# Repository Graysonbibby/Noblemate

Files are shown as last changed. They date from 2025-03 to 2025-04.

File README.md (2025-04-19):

# NobleMate (Automated Voice Controlled Chess Game)
- ### Project Contributors Include: Saud Amjad, Grayson Bibby, Hamzah Nadeem, Kunj Patel, Megh Patel, Nihar Trivedi

**Project Description:** Over the past semester, our team, NobleMate, had designed a voice-controlled, completely automated chess game system against Stockfish.  Our focus being hands-free control with minimal intervention from the user, utilizing an X-Y Coordinate Mechanical Gantry system with an electromagnet for autonomous movement. Each chess piece was 3D printed with slots for magnets at the base. You say your moves by speaking into the microphone when prompted, saying "Pawn from C2 to C3" and this data is serially communicated to the gantry system. You can select your colour (White/Black) and can choose a difficulty (Easy, Medium, Difficult, Insane)
# --------------------------------------------------
- Note: main.cpp and Makefile are given as well
### Documentation + Comprehensive BOM

- Final Design Specification Report Outlines full design implementation + design considerations 
- Page 60 outlines the full BOM of the project

### PCB (Altium Designer files)
- PCB design for a 12V/5V DC-DC buck converter in the shape of a chess piece. You are going from the 12V wall supply and powering the Arduino Uno, Raspberry Pi, and Electromagnet all from this PCB

### Voice Recognition (Python - Requires SpeechRecognition, google-cloud-speech, difflib)

- For the recognizer: Google Cloud Speech-To-Text v1 REST API or Google Web Speech API is sufficient for this project. Google Cloud will require Application Default Credentials to be defined on your system. This is easily doable with a Google Account and downloading Google SDK. 
- All of the voice recognition code is under "chess_voice.py" in the Final Code Folder and the function is then called in a C++ environment using "voiceCommand.cpp" (Requires "voiceCommand.hpp")
- This will require WiFi and the code will be on the Raspberry Pi

### Gantry Movement (Embedded C++ - Code for Arduino Uno)

- This code is developed for the required stepper motor control for the Gantry System. The code was developed using the Arduino Uno IDE

### Chess Game Logic and Functionality (C++)

- Largely developed this ourself and the required code is in the Final Code folder. 
- REST API for Stockfish was used 
- We used https://github.com/awsomeCStutorials/chess-game/blob/master/README.md as a reference for a starting point, but wrote all the C++ code ourselves
- Files include (chess_board, stockfish_service, FENConverter, main, pieces)
- Stockfish is running locally on the Raspberry Pi

### Serial Communication 

- This project utilized a Raspberry Pi 3 Model B for the Chess Logic/Game functionality and an Arduino Uno for the Gantry System Control
- Sends a 7 digit number to the Arduino -> First four digits are the initial and end coordinates of the piece of interest, Final three digits are corresponding flags for special moves, etc.

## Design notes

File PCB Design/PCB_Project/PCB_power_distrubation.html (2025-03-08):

Altium customize

# Board Information Report

Date: | | 2025-03-07
Time: | | 11:34:49 PM
Elapsed Time: | | 00:00:00
Filename: | | C:\Users\Kunj_\OneDrive\Documents\GitHub\Noblemate\PCB Design\PCB_Project\PCB_power_distrubation.PcbDoc
Units: | | mmmils

## Contents

Contents

Board Specification

General

## Board Specification

General
Board Size | 53.2548mm x 80.2548mm
Components on board | 14

Back to top

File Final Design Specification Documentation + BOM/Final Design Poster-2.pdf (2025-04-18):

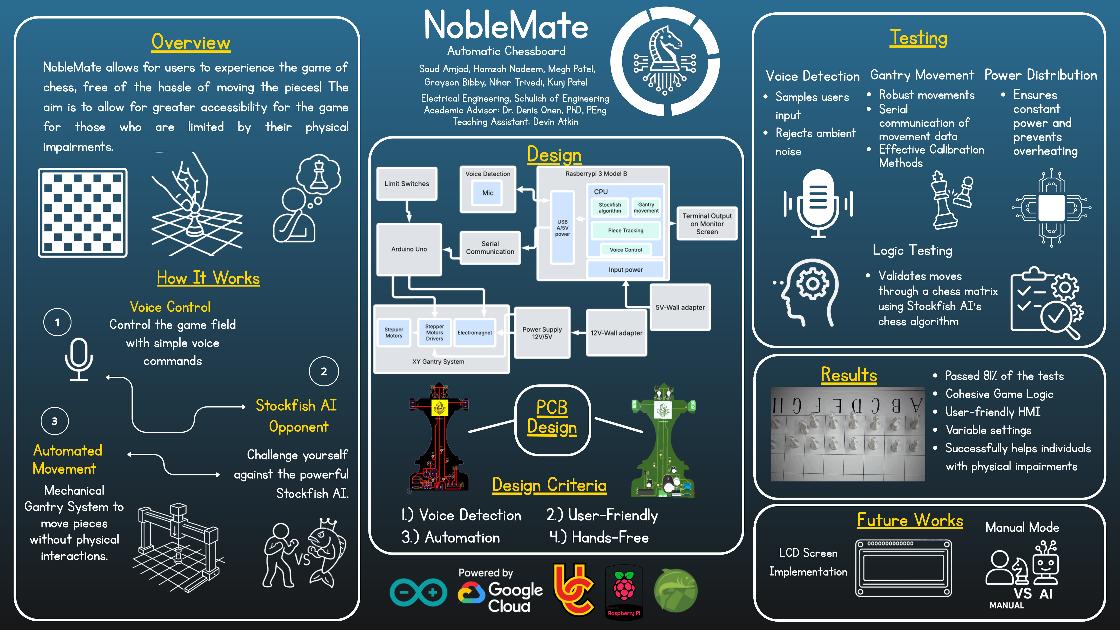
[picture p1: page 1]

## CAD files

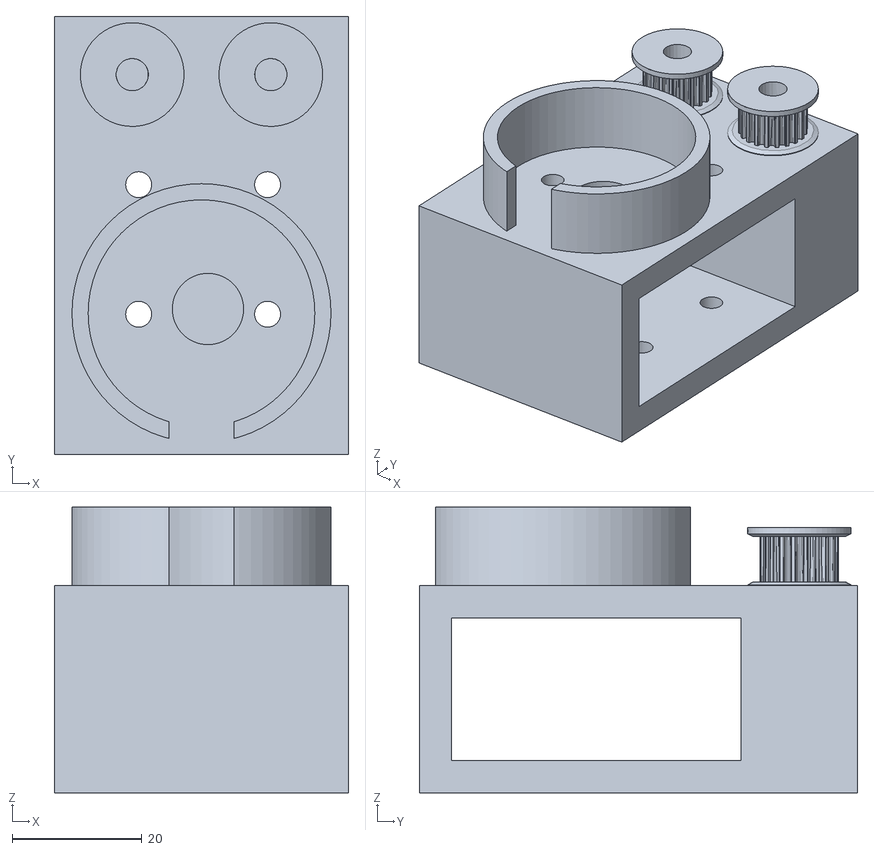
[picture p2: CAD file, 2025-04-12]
3D Files/Middle Rail Blocks_Electromagnet.stl
45.4 x 67.7 x 44.1

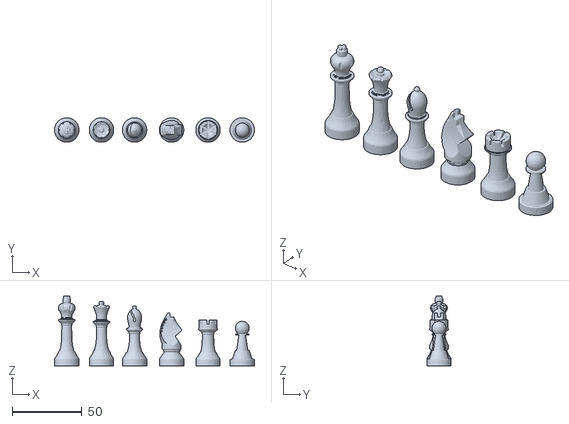
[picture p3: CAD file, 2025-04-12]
3D Files/Chess Set.stl
143.0 x 17.5 x 50.0

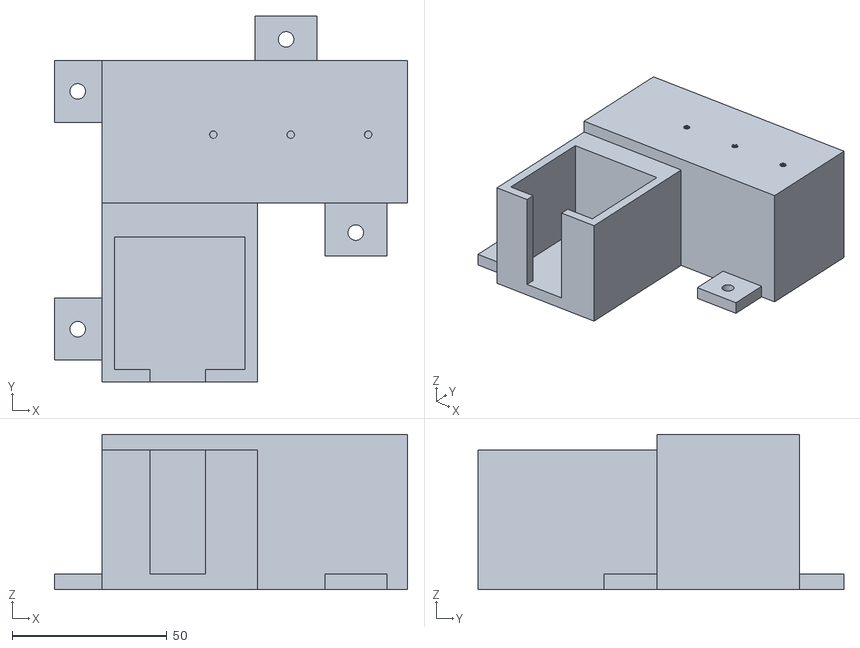
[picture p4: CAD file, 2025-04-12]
3D Files/Support Blocks_Motor.stl
114.0 x 118.1 x 50.1

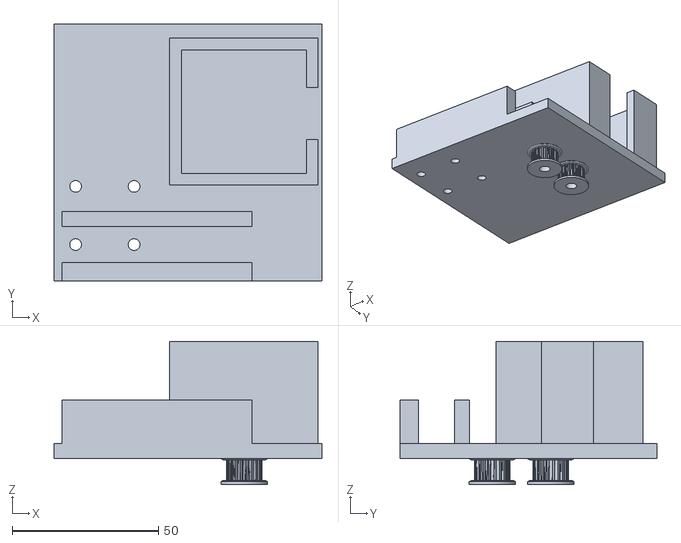
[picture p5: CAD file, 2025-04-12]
3D Files/Middle Rail Blocks_Motor.stl
91.7 x 88.0 x 49.0

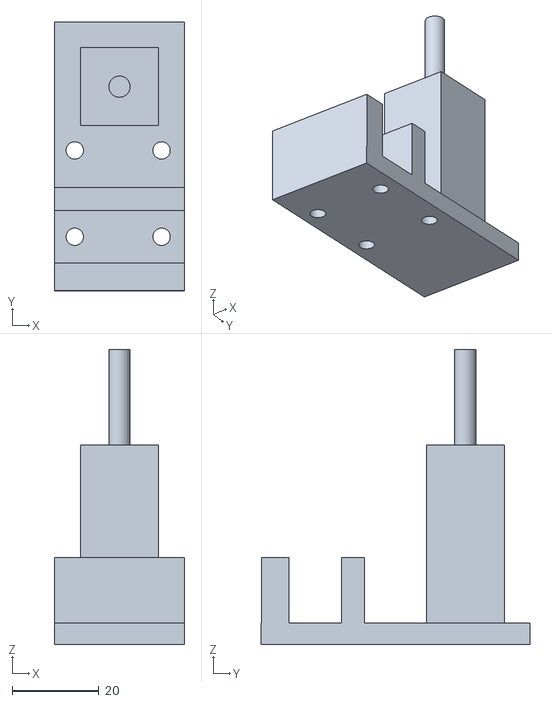
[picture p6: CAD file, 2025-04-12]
3D Files/Middle Rail Blocks_Shaft.stl
30.0 x 62.0 x 68.0

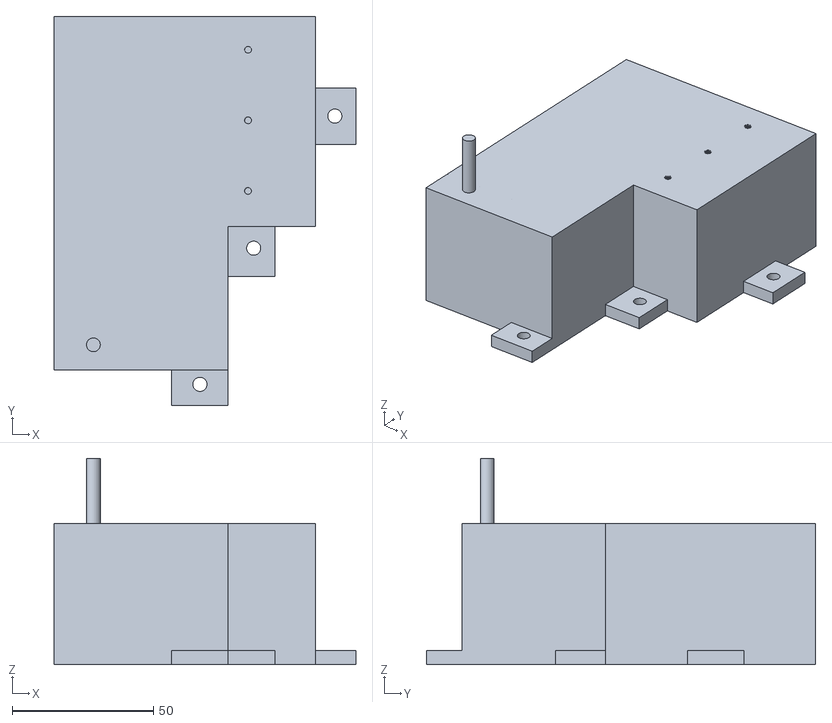
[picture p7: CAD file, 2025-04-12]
3D Files/Support Blocks_Shaft.stl
107.0 x 137.8 x 73.1

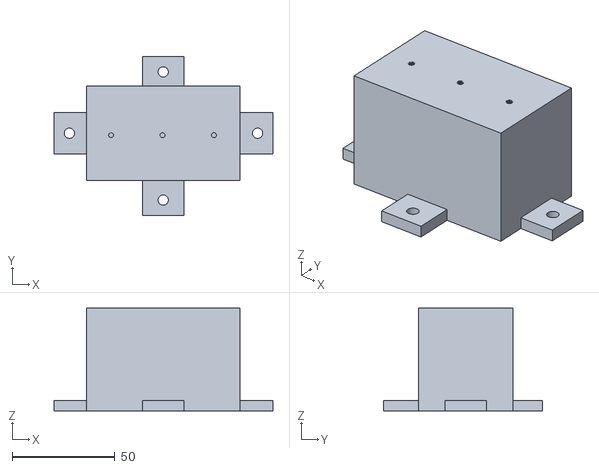
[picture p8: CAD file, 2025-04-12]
3D Files/Support Blocks_Regular.stl
106.6 x 77.3 x 50.1

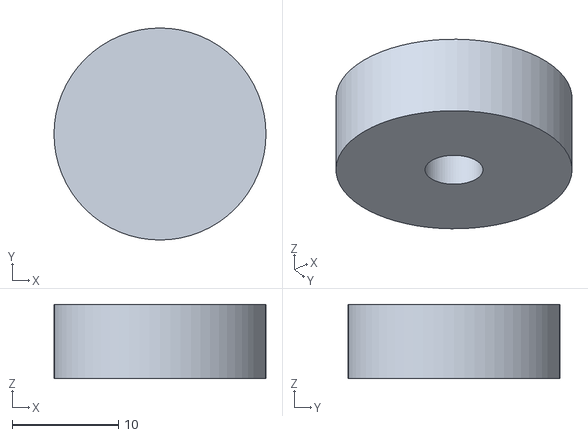
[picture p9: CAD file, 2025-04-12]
3D Files/Middle Rail Blocks_Cap.stl
20.0 x 20.0 x 7.00

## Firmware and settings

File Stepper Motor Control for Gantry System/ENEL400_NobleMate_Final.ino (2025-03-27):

//For Motor to Motor Controller:
//Red = Yellow
// Green = Gray

#include <Stepper.h>
#include <stdlib.h>

const int stepsPerRevolution = 200;  
const int electromagnetPin = 12;
const int x_cal_Pin = 14;
const int y_cal_Pin = 15;
const int x_cal_Pin2 = 16;
const int y_cal_Pin2 = 17;
float fix = 0.85;

// Initialize the stepper motors
Stepper myStepper1(stepsPerRevolution, 8, 9, 10, 11);
Stepper myStepper2(stepsPerRevolution, 2, 3, 4, 5);

// Function to disable stepper motors (idle state)
void setStepperIdle(int no1, int no2, int no3, int no4) {
  digitalWrite(no1, LOW);
  digitalWrite(no2, LOW);
  digitalWrite(no3, LOW);
  digitalWrite(no4, LOW);
}

// Function to turn on/off the electromagnet
void electromagnetControl(int control) {
  if (control == 1) {
    digitalWrite(electromagnetPin, HIGH);
  } else {
    digitalWrite(electromagnetPin, LOW);
  }
}

// Function to move the gantry in a square
void SquareMovement() {
  myStepper1.step(stepsPerRevolution * 3);
  setStepperIdle(8, 9, 10, 11);
  delay(1000);
  myStepper2.step(stepsPerRevolution * 3);
  setStepperIdle(2, 3, 4, 5);
  delay(1000);
  
  myStepper1.step(stepsPerRevolution * 3);
  setStepperIdle(8, 9, 10, 11);
  delay(1000);
  myStepper2.step(stepsPerRevolution * 3);
  setStepperIdle(2, 3, 4, 5);
  delay(1000);
}

// Calibration function for both axes
void calibrateGantry() {

  while (digitalRead(x_cal_Pin) == HIGH) {
    myStepper1.step(1);
  }
  setStepperIdle(8, 9, 10, 11);  // Stop X motor

  delay(500);

  // while (digitalRead(y_cal_Pin) == HIGH) {
  //   myStepper2.step(1);
  // }
  // setStepperIdle(2, 3, 4, 5);  // Stop Y motor

  // delay(500);

  while (digitalRead(x_cal_Pin2) == HIGH) {
    myStepper1.step(-1);
  }
  setStepperIdle(8, 9, 10, 11);  // Stop X motor

  delay(500);

  while (digitalRead(y_cal_Pin2) == HIGH) {
    myStepper2.step(-1);
  }
  setStepperIdle(2, 3, 4, 5);  // Stop Y motor

  delay(500);

}

int row, col;  // Global variables
int row_sign, col_sign;

// Function to calculate movement
void movements(int r_start, int c_start, int r_end, int c_end) {
  row = r_end - r_start;
  col = c_end - c_start;
  if (row == 0) {
    row_sign = 0;
  } else{
    row_sign = row / abs(row);
  }
  if (col == 0) {
    col_sign = 0;
  } else{
    col_sign = col / abs(col);
  }
}

void setup() {
  pinMode(x_cal_Pin, INPUT_PULLUP);  // X-axis switch
  pinMode(y_cal_Pin, INPUT_PULLUP);  // Y-axis switch
  pinMode(x_cal_Pin2, INPUT_PULLUP);  // X-axis switch
  pinMode(y_cal_Pin2, INPUT_PULLUP);  // Y-axis switch
  pinMode(electromagnetPin, OUTPUT);
  
  myStepper1.setSpeed(175);
  myStepper2.setSpeed(175);
  
  Serial.begin(9600);

  electromagnetControl(0);

  // Call the function once in setup to calibrate both X and Y
  calibrateGantry();

}

void loop() {

  electromagnetControl(0);

  //movements(0, 2, 0, 2);

  myStepper1.step(stepsPerRevolution * 2);
  setStepperIdle(8, 9, 10, 11);
  delay(1000);
  myStepper2.step(stepsPerRevolution * 2 * fix);
  setStepperIdle(2, 3, 4, 5);
  delay(1000);

  electromagnetControl(1);

  // movements(4, 5, 4, 6);

  // Movement for knight
  myStepper1.step(stepsPerRevolution * 0.5 * (fix + 0.05));
  setStepperIdle(8, 9, 10, 11);
  delay(1000);
  myStepper2.step(stepsPerRevolution * (2 - 0.5) * fix);
  setStepperIdle(2, 3, 4, 5);
  delay(1000);
  
  myStepper1.step(stepsPerRevolution * (1 - 0.5) * (fix + 0.2));
  setStepperIdle(8, 9, 10, 11);
  delay(1000);
  myStepper2.step(stepsPerRevolution * 0.5 * (fix + 0.2));
  setStepperIdle(2, 3, 4, 5);
  delay(1000);

  electromagnetControl(0);


  // // Movement for chess pieces
  // myStepper1.step(stepsPerRevolution * row_sign * 0.5);
  // delay(1000);
  // setStepperIdle(8, 9, 10, 11);
  // myStepper2.step(stepsPerRevolution * col_sign * (abs(col) - 0.5));
  // setStepperIdle(2, 3, 4, 5);
  // delay(1000);
  
  // myStepper1.step(stepsPerRevolution * row_sign * (abs(row) - 0.5));
  // setStepperIdle(8, 9, 10, 11);
  // delay(1000);
  // myStepper2.step(stepsPerRevolution * col_sign * 0.5);
  // setStepperIdle(2, 3, 4, 5);
  // delay(1000);

  

  // myStepper1.step(stepsPerRevolution * row * fix);
  // setStepperIdle(8, 9, 10, 11);
  // delay(1000);
  // myStepper2.step(stepsPerRevolution * col * fix);
// setStepperIdle(8, 9, 10, 11);
  // delay(1000);

  // myStepper1.step(-stepsPerRevolution * 4);
  // setStepperIdle(8, 9, 10, 11);
  // delay(1000);
  // myStepper2.step(-stepsPerRevolution * 4);
  // setStepperIdle(2, 3, 4, 5);
  // delay(1000);

  // electromagnetControl(0);

  // SquareMovement();

  // electromagnetControl(1);

  // SquareMovement();

  // calibrateGantry();

  while(true){}
}

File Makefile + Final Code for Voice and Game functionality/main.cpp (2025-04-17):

#include "stockfish_service.hpp"
#include "serial_communication.hpp"
#include "chess-board.hpp"
#include "voiceCommand.hpp"
#include "Python.h"
    
#include <iostream>
#include <fcntl.h>
#include <termios.h>
#include <unistd.h>
#include <cstring>

/////////////////////////////////////////////////////////////////////////////////////////////////////
/////////////////////////////////////////////////////////////////////////////////////////////////////
    // Main game loop.
int main() {
    
    chessBoard chess;
    std::vector<std::vector<FENChar>> FENChar_chessboard;
    std::vector<SafeSquares> safesquares;
    std::string FENBoard;

    Coords startCoords;
    Coords endCoords;
    Move move;
    
    FENChar_chessboard = chess.chessBoardView();
    safesquares = chess.get_safeSquares();
    
    FILE* orig_stderr = stderr;
    freopen("/dev/null", "w", stderr);
    
    std::string gameDifficulty = "";
    std::string ELO = "";
    std::string search_depth = "";
    std::string command = "";
    
    bool rematch = false;
    std::string playerColor = "";
    std::string color;
    
    int run = initializeComm();
    
    Py_Initialize();
    
    bool replayGame = false;
    
    while(true){
        
        if(!rematch){
            gameDifficulty = voiceInput("get_game_mode");
            std::cout << "selected difficulty: " << gameDifficulty << std::endl;
            if(gameDifficulty == "Easy"){
                ELO = "1200";
                search_depth = "10";
            } else if (gameDifficulty == "Medium"){
                ELO = "1800";
                search_depth = "11";
            } else if (gameDifficulty == "Difficult"){
                ELO = "2400";
                search_depth = "12";
            } else if (gameDifficulty == "Insane"){
                ELO = "3200";
                search_depth = "13";
            } else {
                ELO = "1200";
                search_depth = "10";
            }
            
            //end of ELO setting functionality
            std::cout << "ELO: " << ELO << std::endl;
         
            std::cout << "Enter which colour you wish to play as (white or black): \n";
            color = voiceInput("get_player_color");
            chess.set_Colors(color);
            
            if(chess.get_UserColor() == White){
                playerColor = "white";
            } else {
                playerColor = "black";    
            }
            //end of getting player colour functionality
        }
        
        std::cout << "Player playing as: " << playerColor << "\n";
        std::cout << "game difficulty : " << ELO << std::endl;
        
        if(replayGame){
            int i = 30;
            //30 second countdown timer
            while(i >= 0){
                std::cout << "Countdown to replay: ";
                std::cout << i << " ";
                sleep(1);
                i--;
            }
            std::cout << "\n";
        }

        chess.reset_board();
        
        while (true) {
            // Initialize the Python Interpreter
            FENBoard = chess.get_FENBoard();
            FENChar_chessboard = chess.chessBoardView();
            safesquares = chess.get_safeSquares();
        
            //printing the chessboard
            for (int i = chess.getChessBoardSize(); i > 0; i--){
                for (int j = 0; j < chess.getChessBoardSize(); j++){
                    std::string str(1, FENChar_chessboard[i-1][j]);
                    std::cout << str << " ";
                }
                std::cout << i << "\n";
            }
        
            std::cout << "A B C D E F G H";
            std::cout << "\n";
        
            //getting the move from either the user or stockfish
            if (!chess.get_isGameOver() && (chess.get_playerColor() == chess.get_UserColor())){
                /*command = voiceInput("get_command");
                if(command == "View"){
                    sleep(15);
                }*/
                std::cout << "Enter Move: ";
                
                move = moveInput();
                startCoords = voiceCommandProcessing(move.startSquare);
                endCoords = voiceCommandProcessing(move.endSquare);

                std::string dig1 = std::to_string(startCoords.y);
                std::string dig2 = std::to_string(startCoords.x);
                std::string dig3 = std::to_string(endCoords.y);
                std::string dig4 = std::to_string(endCoords.x);
                
                chess.set_moveCoords("");
                chess.set_moveCoords(dig2 + dig1 + dig4 + dig3);
                chess.move(startCoords.y-1, startCoords.x-1, endCoords.y-1, endCoords.x-1);
                
                std::cout << startCoords.y-1 << ", " <<  startCoords.x-1 << ", " << endCoords.y-1 << ", " << endCoords.x-1;
                std::cout << "\n";
            } 
            else if (!chess.get_isGameOver() && (chess.get_playerColor() == chess.get_EngineColor())) {
                std::vector<Coords> engineMove;
                std::string fenboard = chess.get_FENBoard();
                char promotedPiece = 'q';
            
                engineMove = get_bestMove(fenboard, ELO, search_depth, &promotedPiece);
                
                std::string dig1 = std::to_string(engineMove[0].x+1);
                std::string dig2 = std::to_string(engineMove[0].y+1);
                std::string dig3 = std::to_string(engineMove[1].x+1);
                std::string dig4 = std::to_string(engineMove[1].y+1);
                
                chess.set_moveCoords("");
                chess.set_moveCoords(dig1 + dig2 + dig3 + dig4);
                
                chess.set_enginePromotedPiece(promotedPiece);
                chess.move(engineMove[0].y, engineMove[0].x, engineMove[1].y, engineMove[1].x);
                
            }
            else {
                break;
            }
        }
        std::cout << chess.get_gameOverMessage() << "\n";
        
        std::string rematchOption = voiceInput("get_reset_condition");
        
        if(rematchOption == "Rematch"){
            rematch = true;
            if(playerColor == "white") {
                chess.set_Colors("Black");
                playerColor = "black";
            }
            else {
                chess.set_Colors("White");
                playerColor = "white";
            }
            std::cout << "Game rematch initiated!\n";
            
        } else {
            rematch = false;
            std::cout << "Returning to game menu!\n";
        }
        
        replayGame = true;
        
    }//end outer while loop
    
    Py_Finalize();
    
    return 0;
}

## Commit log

2025-02-21 Add files via upload
    chess-board contains main function with some code to test everything
2025-03-05 Create Power distribution for Noblemate Schematic Layout.SchDoc
    [Power distribution for Noblemate Schematic Layout.SchDoc]
2025-03-05 Update to PCB File
    [Power distribution for Noblemate Schematic Layout.SchDoc]
2025-03-06 Update Power distribution for Noblemate Schematic Layout.SchDoc
    [Power distribution for Noblemate Schematic Layout.SchDoc]
2025-03-07 PCB project file
    [PCB_Project.PrjPcb, Power distribution for Noblemate Schematic Layout.SchDoc]
2025-03-07 PCB circuit Validated
    [PCB_Project.PrjPcb, Power distribution for Noblemate Schematic Layout.SchDoc]
2025-03-07 Final Version of Schematic
    [Power distribution for Noblemate Schematic Layout.SchDoc]
2025-03-08 Update with only through hole compnents
    [PCB_Project.PrjPcb, Power distribution for Noblemate Schematic Layout.SchDoc]
2025-03-08 PCD Layout without Traces
    [PCB_Project.PrjPcb, PCB_power_distrubation.PcbDoc, Power distribution for Noblemate Schematic Layout.SchDoc]
2025-03-08 PCB trace Complete
    [PCB_power_distrubation.PcbDoc]
2025-03-08 PCB Traces Completed (Positive ones)
    [PCB_power_distrubation.PcbDoc]
2025-03-08 PCB traces with GND
    Added GND points
    [PCB_power_distrubation.PcbDoc]
2025-03-08 name update
    [PCB_power_distribution.PcbDoc]
2025-03-08 use VSCode x64 compiler 2022 for windows
    Run the following line to compile the code:
    cl.exe /EHsc chess-board.cpp FENConverter.cpp /link /LIBPATH:"C:\Users\bibby\anaconda3\pkgs\python-3.9.12-h6244533_0\libs"
    (obviously change the python-3.9.12 package location)
    After compiling, all you have to do is type in the executable file name with .exe at the end.
2025-03-09 PCB update with New traces
    [NEw.PcbDoc, PCB_power_distribution.PcbDoc]
2025-03-09 NEW STYLEEE
    [King Shape PCB.PcbDoc, NEw.PcbDoc]
2025-03-09 New Design for PCB (maybe)
    [King Shape PCB.PcbDoc, PCB_Project.PrjPcb]
2025-03-10 NEW PCB DESIGNNNNNN!!!
    [King Shape PCB.PcbDoc]
2025-03-10 new name
    [PCB_OLD.PcbDoc]
2025-03-11 Stepper Motor Control
    ChessMovingV1 is most recent
    Other two are reference files
2025-03-12 NEW PCB
    [King Shape PCB.PcbDoc, New_PCB.PcbDoc, PCB_Project.PrjPcb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]
2025-03-12 Pcb new
    [PCB_Project.PrjPcb, Power distribution for Noblemate Schematic Layout.SchDoc]
2025-03-13 PCB FILE
    [New_PCB.PcbDoc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]
2025-04-12 3d Files
    All STL Files of most current iterations used in project.
    [Chess Set.stl, Middle Rail Blocks_Cap.stl, Middle Rail Blocks_Electromagnet.stl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]
